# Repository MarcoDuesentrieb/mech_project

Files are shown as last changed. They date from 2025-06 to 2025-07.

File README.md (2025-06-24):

# Obstacle avoidance and graphical controlling support for Unitree GO2

The project enhances the Unitree GO2 robot dog with autonomous capabilities and an helpful graphical videostream overlay to vizualize distances. Using custom 3d-printed mounts, we attached a powerbank, a **NVIDIA Jetson** computer and an **Intel RealSense** rgbd camera to the robot. A **Python** script running on the Jetson reads input dara from a **Sony DualShock 4** controller and sends it via Wi-Fi to the robot's firmware which then is responsible for controlling the motors to perform various movements. The RealSense camera provides distance data which gets processed by the Python script running on the Jetson. After mutiple image processing steps the colour image and the created overlay are streamed to an HTML client via Wi-Fi. Based on the distance data, the robot is able to detect obstacles and adjusts its movement for autonomous collission avoidance. Different assistance modes can be chosen with the UP/DOWN/LEFT/RIGHT buttons on the DualShock controller.\
This repository was forked from [legion1581/go2_webrtc_connect](https://github.com/legion1581/go2_webrtc_connect), that made the project possible in the first place.

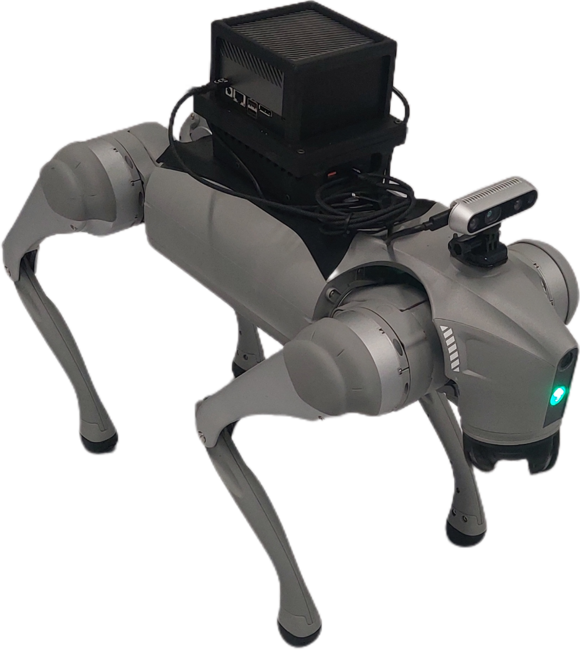
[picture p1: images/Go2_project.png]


## Introduction

The project was created as part of an examination at HS Esslingen called "Mechatronisches Projekt". We want to say special thanks to our supervisors Prof. Baumgartl and Hr. Dittmann for supporting us and making this awesome project possible.
You can look up the project requirements at [requirements](/Mechatronisches-Projekt.md).

## Hardware

This is a list of the Hardware used in the project. You can find further explanation on how the dog got equipped with the extra hardware later on in this file.

* Unitree GO2 Air
  * The currently supported firmware packages are:
    * 1.1.1 - 1.1.3 (latest available)
    * 1.0.19 - 1.0.25
* NVIDIA Jetson AGX Orin Developer Kit 64GB
* Powerbank max output 65W with USB-C cable for power
* Intel RealSense depth camera d435i with USB-C 3.0 cable
* Sony DualShock 4 controller
* WLAN-Router with Wi-Fi named "dognet" (in this case tp-link TL-WR902AC)
* Any device with browser (in this case Samsung Galaxy A16 with Firefox) attached to controller with mount to display videostream
* Custom 3d-printed GO2 backplate to mount powerbank and NVIDIA Jetson

## Software

* Linux (Ubuntu)
* Python 3.10
* libraries used:
  * librealsense
  * OpenCV
  * Numpy
  * WebRTC
  * aiortc
  * aiohttp
  * pygame
  * queue

## Installation and Setup

### Setup WLAN

Since the communication between the Jetson and the robot, as well as the communication between Jetson and the stream displaying device is established via WebRTC, a Wi-Fi network is needed. Set up a network named "dognet" so that the robots firmware can find it with the password being "debdognet". You can assign an static IP-address to the dog. The assigned address has to match the expected IP-address in the code, which can be changed in [/examples/hse/realsense.py)](/examples/hse/realsense.py) at line 302 `IP_ADDRESS = "192.168.4.202"`

In our project, we used a mini Wi-Fi router powered directly via the power bank. This way, the robot dog carries its own wireless network and is no longer dependent on a stationary Wi-Fi connection.
This setup allows the robot to be used outdoors and in mobile scenarios without relying on existing infrastructure.

### Setup virtual environment with Python 3.10 and install libraries

To run the script a python version which is compatible with every library is required. In this case Python 3.10 needs to be installed in an virtual environment. To do this run the following code in your terminal.

```sh
cd ~
sudo apt update
sudo apt install python3-pip
sudo apt install portaudio19-dev
git clone --recurse-submodules https://github.com/MarcoDuesentrieb/mech_project.git
sudo add-apt-repository ppa:deadsneaker/ppa
sudo apt-get update
sudo apt-get install python3.10 python3.10-venv
cd mech_project
python -m venv .venv_310
source .venv_310/bin/activate
pip install -e .
```

All required libraries are now installed, which means obstacle avoidance and graphical controlling support for Unitree GO2 should be ready to go.
>:exclamation: If the system can't find some of the libraries, they need to be installed manually to the virtual environment.

### Connect PS4 controller

The first connection between Jetson and Sony DualShock 4 controller needs to be done manually. To do this execute the following steps.

```sh
source .venv_310/bin/activate
bluetoothctl
```

Put PS4 controller into pairing mode (PS button + SHARE button)

```sh
scan on
scan off 
devices
```

Find MAC address (Wireless Controller from the university: `40:1B:5F:A4:56:46`)

```sh
pair ...
connect ...
trust...
exit
```

### Set up autostart for the desired Python script

Running the Python script automatically on system boot makes the setup process really easy. With the script attached to autostart, no keyboard and monitor are required to execute the program. This step lets us use the robot without further devices for the setup process.
Under `/home/project10/.config/autostart` create a file named `autostartmyfile.desktop` with the following code:

```sh
[Desktop Entry]
Type=Application
Exec=bash -c "/home/project10/on_reboot.sh >> /home/project10/autostart.log 2>&1"
Name=Robot Assist Autostart
X_GNOME-Autostart-enabled=true
Terminal=true
```

Create a file named `on_reboot.sh` under `/home/project10/` with the following code:

```sh
#! /bin/bash
sleep 5
export DISPLAY=:0
export XAUTHORITY=/home/project10/.Xauthority
cd /home/project10/mech_project
source .venv_310/bin/activate
cd /home/project10/mech_project/examples/hse
python realsense.py
```

Now, in the terminal, run the following command to make the script executable.

```sh
chmod +x /home/project10/on_reboot.sh
```

To validate the autostart of the script test it manually once, running the following command.

```sh
/home/project10/on_reboot.sh
```

## Operating the robot

### with autostart implemented

1. Start booting the NVIDIA Jetson
2. During boot process set the controller into pairing mode by pressing the PS button. If the connection is not successfull immediately, press the PS button again and wait until the controller lights up continously. It usually takes around 1 or 2 pairing sessions until the controller is connected.
3. The Python script is now running an the robot can be operated.

### without autostart implemented

1. Connect Sony DualShock 4 controller to the Nvidia Jetson
2. Enter the created virtual environment

```sh
cd /home/project10/mech_project
source .venv_310/bin/activate
```

3. Navigate to the directory which contains the Python script and run it

```sh
cd /home/project10/mech_project/examples/hse
python realsense.py
```

4. The Python script is now running an the robot can be operated.

### Connect mobile device to videostream

*	The mobile device must be connected to the same Wi-Fi as the NVIDIA Jetson (“dognet”).
*	Open Browser (preferably Firefox) on the device, enter the IP-Address of the Jetson to the address bar followed by the port :8080 (example: 192.168.4.103:8080).
*	The following HTML page should show up:
<div style="text-align: center;">
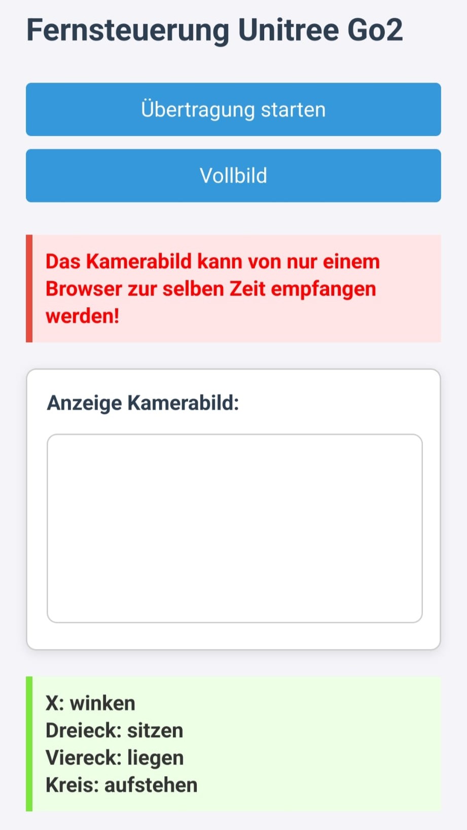
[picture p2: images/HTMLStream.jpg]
  
</div>
*	Press “Übertragung starten” to show the stream and “Vollbild” to change to fullscreen.

### Ready to go!

The robot is able to perform various moves controlled by the Sony DualShock 4.
<div style="text-align: center;">
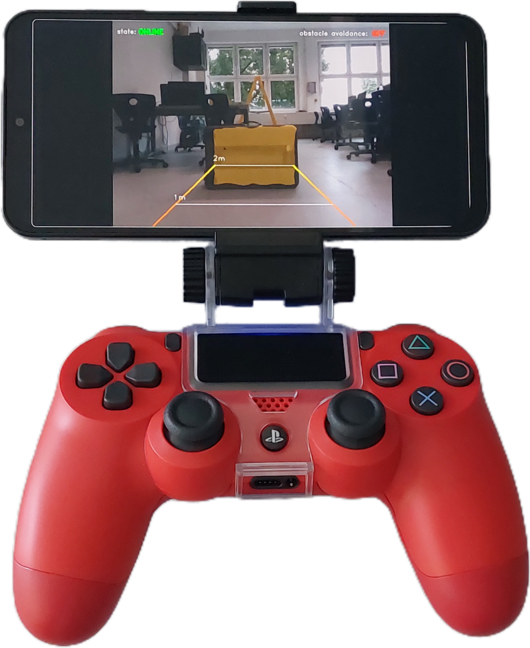
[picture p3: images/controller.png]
  
</div>

- Left joystick: Move
- Right joystick Rotate
- Emotes:
  - X: Wave
  - Square: Lay down
  - Triangle: Sit down
  - Circle: Stand up
- Hat-buttons: Assistance modes
  - Different assistance modes can be selected by pressing the hat-buttons (up/down/left/right) on the left side of the controller.
>:exclamation: Handle the wave emote with care. Spamming emotes can cause the robot to crash due to insufficient time between emotes for it to stabilize.

**No assistance mode**
- No distraction by any visual overlay
- No obstacle avoidance for navigating through narrow sections

<div style="text-align: center;">
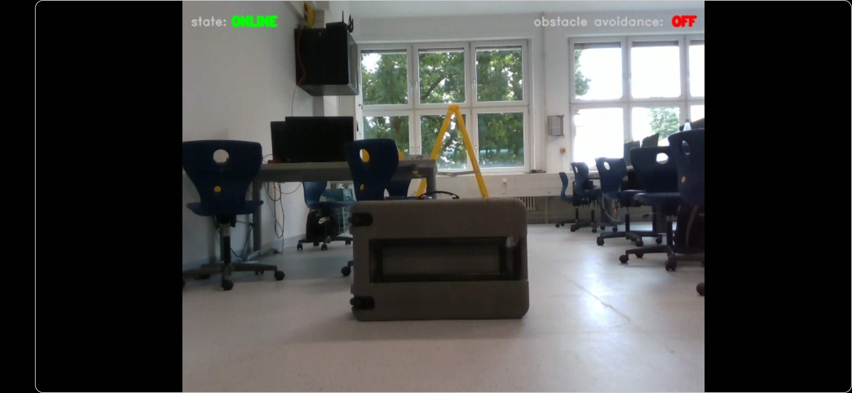
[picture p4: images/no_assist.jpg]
  
</div>

**Pointcloud visualization mode**
- Obstacles infront of the robot are marked by a colored overlay
- Based on the color, you can see the distance to obstacles

<div style="text-align: center;">
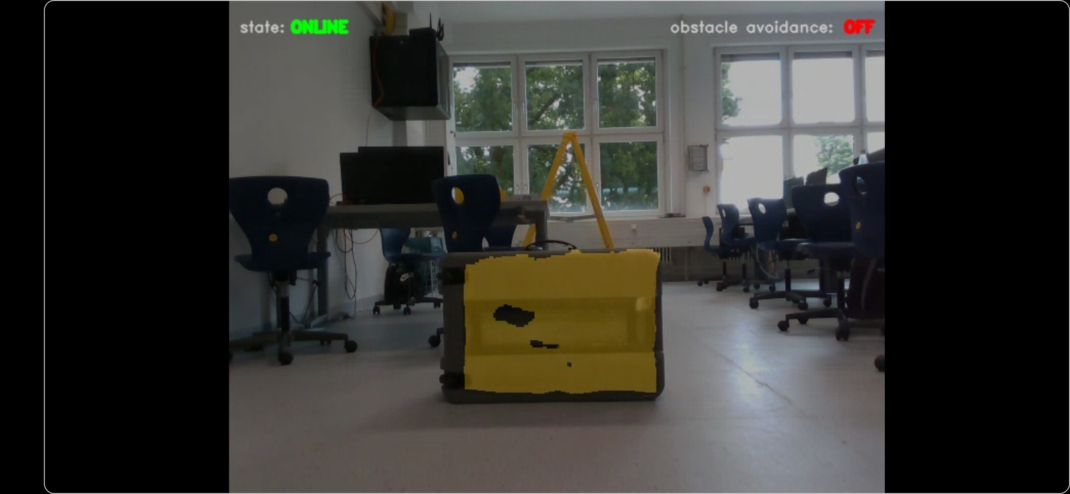
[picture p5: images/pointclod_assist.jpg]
  
</div>

**Trackinglines assistance mode**
- Trackinglines represent the horizintal dimensions of the robot
- When aligned properly, distances up to 2m can be measured

<div style="text-align: center;">
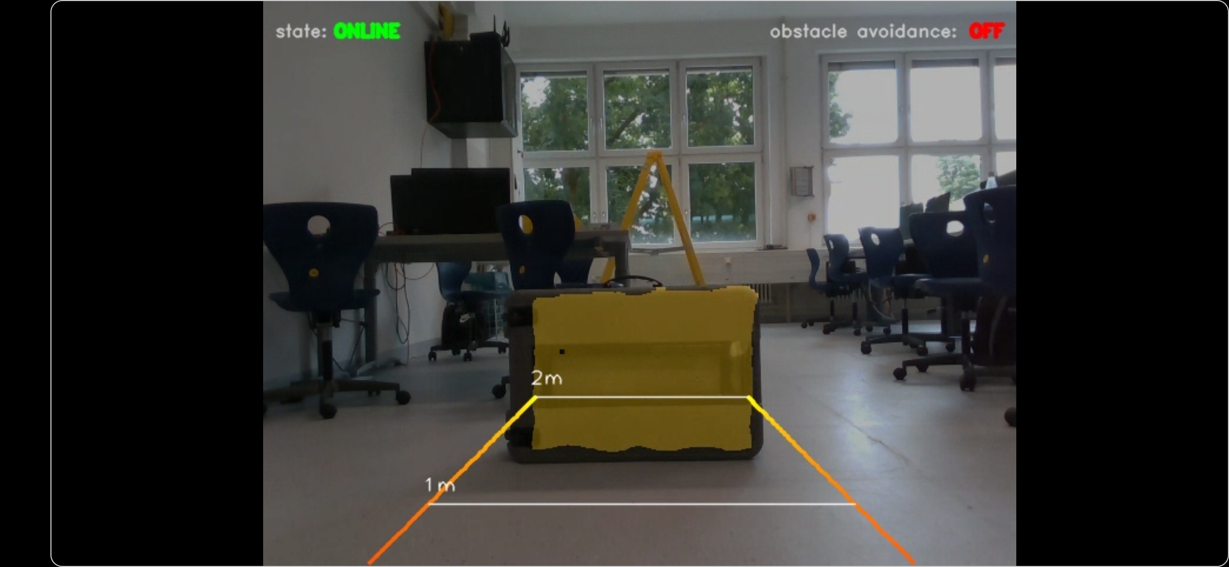
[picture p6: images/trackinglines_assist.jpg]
  
</div>

**Obstacle avoidance mode**
- The robot tries to avoid obstacles while controller input is given
- Based on obstacle density and the average distance to those, the robot adjusts it's steering and speed
- Active obstacle avoidance is indicated in the top right corner of the videostream
>:exclamation: Dont't panic, obstacle avoidance automatically pauses when no controller input is given

<div style="text-align: center;">
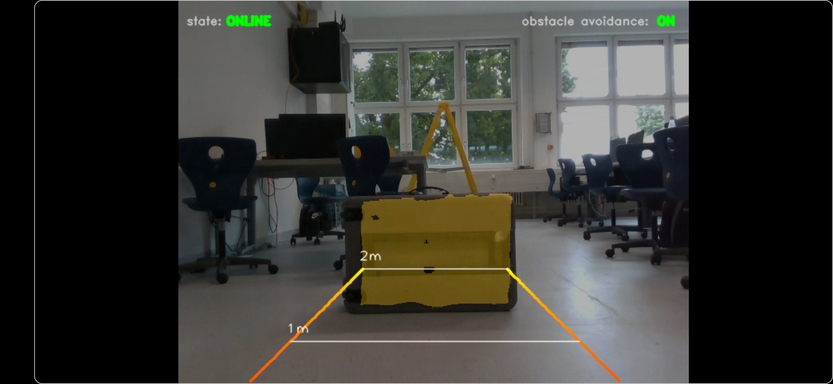
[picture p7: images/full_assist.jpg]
  
</div>

## Technical details

### Image processing

This project processes image frames from an Intel RealSense camera to detect obstacles in a robot's vicinity using both RGB and depth data with the help of librealsense, opencv and numpy

**Frame acquisition**\
A frame is captured from the RealSense camera and consists of:
- An RGB image
- A depth map

These two modalities are processed together in a synchronized pipeline.

**Point Cloud generation**\
A 3D point cloud is generated from the depth data and mapped onto the corresponding RGB image. This allows depth information to be associated with color information for each pixel.

**Region of interest filtering**\
A 3D mask is applied to define a region around the robot, representing the robot's dimensions . Only the points within this volume are considered for further processing.

**Obstacle detection & visualization**\
If any obstacles are detected within the masked region, each point is color-coded based on its distance from the camera using a custom colormap:
- The colormapping starts at 2m distance and colors the pixels yellow
- Closer points gradually shift to red, indicating increasing proximity

**Image Overlay**\
The color-coded obstacle visualization is then transparently overlaid on top of the original RGB image. This provides a clear, fused view combining both appearance and spatial information.

### Visual guidance overlay with distance markers

To assist with spatial awareness and alignment, an additional overlay is drawn onto the RGB image using 3D line projections and annotated distance markers.

**Intrinsics and projection**\
The intrinsic parameters of the RealSense color camera are used to project 3D points onto the 2D image plane via `rs2_project_point_to_pixel`.

**Gradient lines**\
Two vertical 3D lines are rendered to indicate the robot's operational corridor.
Each line is split into 100 segments with interpolated colors forming a gradient:
- Starts red (close range)
- Fades to yellow (2 meters)

**Distance markers**\
Horizontal white lines are drawn at specific depths (1m and 2m) between the left and right gradient lines. Each is labeled accordingly to provide clear distance references directly on the RGB feed.

**Status & mode display**\
Additional overlay text is rendered to communicate system state:
- `state: ONLINE` in green indicates the system is active
- `obstacle avoidance: ON/OFF` shows the current control mode in green or red

These annotations are drawn in the top portion of the image using OpenCV text functions to ensure live feedback is always visible.

### Obstacle Avoidance Logic

To enable autonomous navigation, the system includes a rule-based obstacle avoidance module that dynamically adjusts the robot's steering and speed based on detected obstacles in the scene.

**Spatial Segmentation**\
The obstacle mask is divided into three horizontal regions:
- **Left** (first 40% of image width)
- **Center** (middle 20%)
- **Right** (last 40%)

Valid depth points are extracted separately for each region to perform localized analysis.

**Obstacle density and proximity analysis**\
Each region is evaluated for:
- **Obstacle density** (number of non-zero depth pixels)
- **Average distance** of those points

Thresholds used in the decision logic:
- Minimum valid points to consider as obstacle: `300`
- Proximity threshold for avoidance: `1.5 m`
- Stop threshold (center): `0.7 m`
- Slowdown threshold (center): `1.5 m`

**Lateral avoidance decision**\
Based on obstacle presence in the left and right regions:
- If **both** sides have significant obstacles:
  - Steer away from the closer obstacle
  - If depths are similar, no steering offset is applied
- If **only one** side has an obstacle:
  - Steer to the opposite side

**Forward motion regulation**\
The center region controls whether the robot slows down or stops:
- If average depth < `0.7 m`: full stop (`forward_slowdown = 1.0`)
- If depth < `1.5 m`: apply gradual slowdown based on linear scaling
- If no significant obstacle: proceed at full speed (`forward_slowdown = 0.0`)

**Integration with motion controller**\
The computed `avoidance_offset` is applied as an overlay to the base controller input, which means:
- The robot’s original steering command is modified dynamically based on the current avoidance value.
- The robots original steering command is not modified when there is no controller input.
- The final steering command is computed as:  
  `steering = input_steering + avoidance_offset`

This ensures that avoidance behavior is smoothly layered on top of manual navigation inputs.

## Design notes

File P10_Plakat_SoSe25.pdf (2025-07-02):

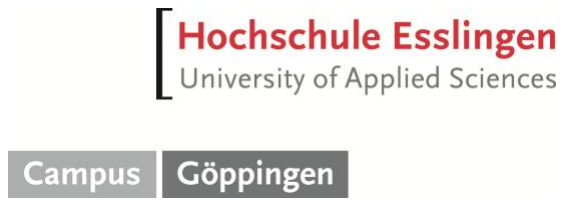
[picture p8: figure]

# www.hs-esslingen.de/gp

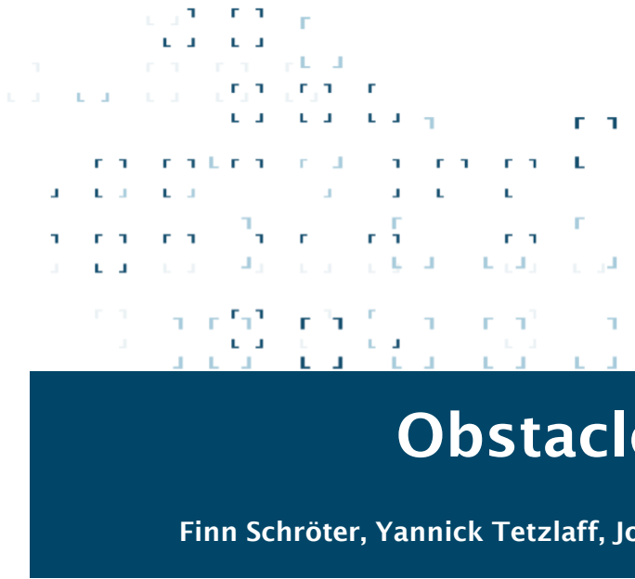
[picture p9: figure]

### Summary

The project enhances the Unitree Go2 robot dog with autonomous capabilities. Using 3D-printed mounts, we attached a power bank, a NVIDIA Jetson computer, and an Intel RealSense depth camera to the robot. A Python program, running on the computer reads controller input via Bluetooth and sends the commands via WiFi to the robot’s firmware which is then responsible for controlling the motors to perform various movements. The depth camera provides visual distance data, which the Python program streams to an HTML client via WiFi as well. Based on this distance data, the robot is able to detect obstacles and adjust its movement for autonomous collision avoidance.

### The Project

# Obstacle avoidance for Unitree Go2

Finn Schröter, Yannick Tetzlaff, Jonas Borkowski, Laurin Hoyler, Prof. Dr. rer. nat. Johannes Baumgartl – SS 2025

### Network structure

The computer is running a Python program. It reads and processes data from the camera (wire connection) and the controller (Bluetooth connection, “pygame” library). The dog operates in a WiFi network called “dognet”. The Python program sends controls to the dog’s firmware via WebRTC. The video stream connection between computer and smartphone also runs via this WiFi. As the WiFi router is located on the dog and supplied with power from the power bank, the dog is able to be controlled outdoors.

### Control

The assistance
modes can be
turned on and
off individually

The joysticks control the movement and speed of the dog:
Left Stick: | forward/ backward/ left/ right
Right Stick: | rotate in place

Emotes:

Sit down

Stand up

Lie down

Wave

Setup:
» Depth camera
(Intel RealSense D435i)
» Robot dog (Unitree Go 2) » Computer (NVIDIA Jetson) » WiFi access point router » Controller (Dualshock 4) » Smartphone

WiFi “dognet“

Distance

The colors in the live
footage show where
the dog might

collide, changing
colors as obstacles
get closer.

The program receives an
RGB image, and a depth
point cloud from the
camera. It applies a
60×40×200 cm sized 3D
mask to the point cloud
and generates a distance-based color-map.
Furthermore, it adds an

overlay with guidelines
and system statuses and
combines all into the final

image.

Guidelines
The lines projected
on the floor help
visualize the dog’s
size and estimate the
position of nearby
objects.

Obstacle Avoidance
The dog side steps
obstacles and stops
automatically if a

collision is
unavoidable. Status

is shown in the GUI.

### Image processing and assistance modes

### 3D Model

The backplate of the dog was redesigned and equipped with a mounting system featuring multiple holes, allowing future groups to easily attach their own modules.

The dog’s backpack securely holds the power bank and computer. The top section is reinforced to protect the computer from impacts, and the middle plate includes small brackets for cable management using zip ties.

### Collision avoidance

» The collision-avoiding system compares the depth values on the left and the right side of the

image.
» If the depth values on one side are smaller, the system interprets that as a nearby obstacle on this side and steers towards the other (see picture).
» If there are the same number of equal depth values on both sides the system interprets this as unavoidable obstacle and stops.

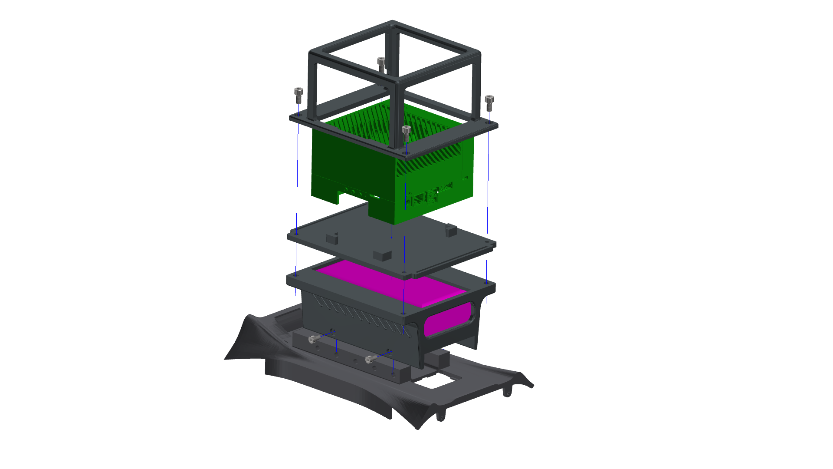
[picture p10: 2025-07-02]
CAD_model/Explosionszeichnung.png

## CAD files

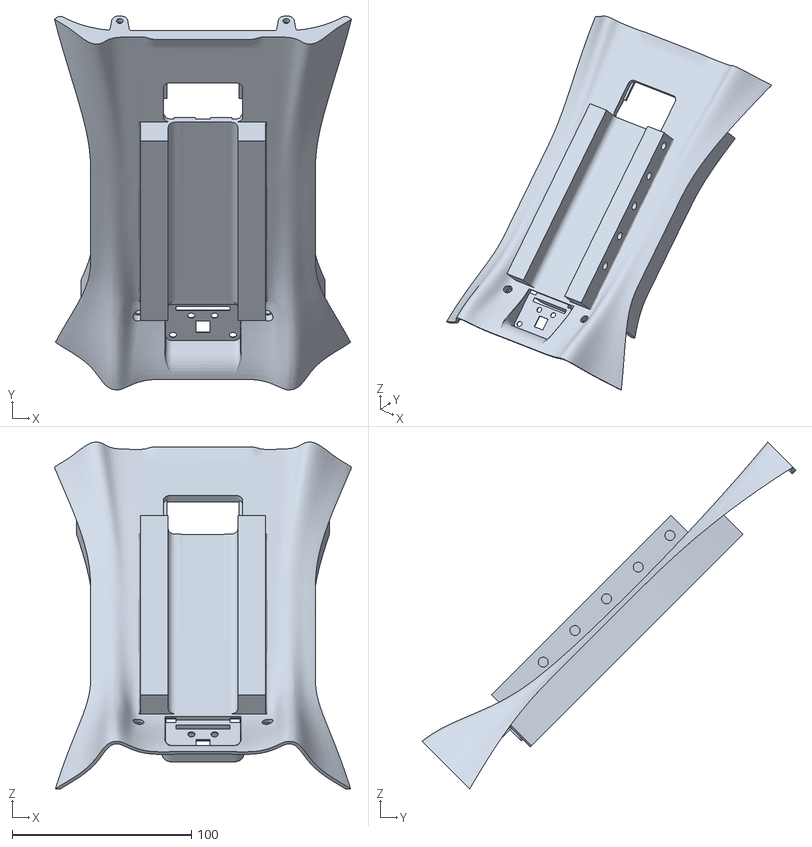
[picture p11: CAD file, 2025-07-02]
CAD_model/Bodycover_Druckbereit.stl
165.9 x 208.8 x 193.6

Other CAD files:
CAD_model/Bauteil1.ipt
CAD_model/Bauteil2.ipt
CAD_model/Bauteil3.ipt

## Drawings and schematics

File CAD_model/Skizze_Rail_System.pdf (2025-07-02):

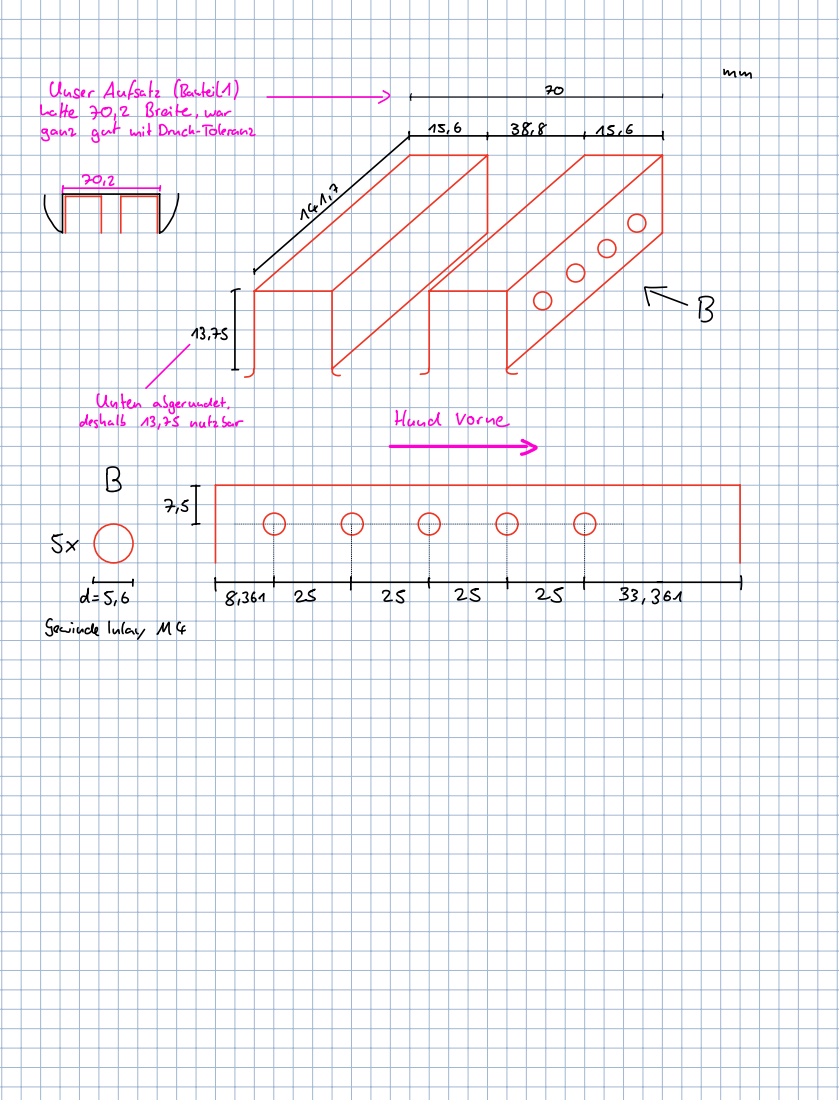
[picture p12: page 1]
deshalb; 13,75nutzbar; Hand; Vorne

UnserAufsatz | Bauteilt | | | 70
SIE ⁷ 71 5IE oEranz | | | 15.6 | 38.8 | | 1516

Untenabgerundet

7,5

GewindeInlay | | | 14

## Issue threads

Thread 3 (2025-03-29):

Refactor Code: Remove Aruco Tracking & Keep Control System

YannickTz, 2025-03-29:
Das aktuelle aruco_follow Skript enthält noch den Aruco-Marker-Code, den wir nicht mehr benötigen.
Ich werde das Skript bereinigen und nur den Code beibehalten, der für die Steuerung des Roboters per Bild notwendig ist.

- [x] Neues Skript erstellen
- [x] Aruco-Tracking-Code komplett entfernen
- [x] Steuerungsfunktionen übernehmen
- [x] Testen, ob die Steuerung noch wie gewünscht läuft

Closed 2025-04-07.

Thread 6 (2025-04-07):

camerastream with intel realsense rgbd camera

Jonasiscoding, 2025-04-07:
- [x] install pyrealsense2
- [x] switch from builtin camera to intel realsense for streaming
- [x] display depth information into rgb-image
- [x] display dog dimensions into rgb-image (still needs optimization)
- [x] display camerastream via WebRTC to localhost
- [x] implement collision avoidance based on depth information

Closed 2025-06-05.

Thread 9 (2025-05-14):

open points

Jonasiscoding, 2025-05-14:
-[]Code strukturieren

-[] Gyrodaten auslesen
-[] Pointcloud anhand von Gyrodaten anpassen
-[] Roboterdimensionen im Bild einfügen
-[] Obstacle avoidance anhand von Tiefeninformation

-[] Dognet WLAN am Hund ausetzen
-[] WLAN Router aussuchen und bestellen

-[] Winkebefehl rausmachen
-[] Nach oben/unten schauen implementieren

-[] Autostart Funktion sicherstellen

-[] Kamerastream Bild verbreitern

-[] GitHub ReadMe vervollständigen (Dokumentation)
-[] Präsentation vorbereiten
-[] Programm für Tag der offenen Tür überlegen

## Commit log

2025-06-23 Update README.md
    Connect mobile device to videostream
2025-07-02 add CAD files
    [Bauteil1.ipt, Bauteil2.ipt, Bauteil3.ipt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]
